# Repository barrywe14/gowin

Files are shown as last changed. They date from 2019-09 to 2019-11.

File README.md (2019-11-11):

# Gowin Project
Dokumentasi Elektronik Produk pertanian Gowin (Dropper Biji Jagung). 

# Rangkaian Elektronik Gowin
Secara general sistem elektrik Gowin
GambarElektronik
Dibawah ini adalah rangkaian di dalam kotak elektronik 
GambarHardware
Rangkaian Elektronik dalam bentuk PDF bisa [klik disini](/circuit/GoWinElectricalv2/GowinController-Controller.pdf)

## Program Arduino
Program Alat bisa klik [disini](/circuit/GoWinElectricalv1/program/GowinScript/GowinScript.ino)
Kemudian program untuk test hardware bisa klik [disini](/circuit/GoWinElectricalv1/program/GowinTestScript/GowinTestScript.ino)
# Foto Dokumentasi
Kontrol, Kotak Elektronik, dan Instrument <br>
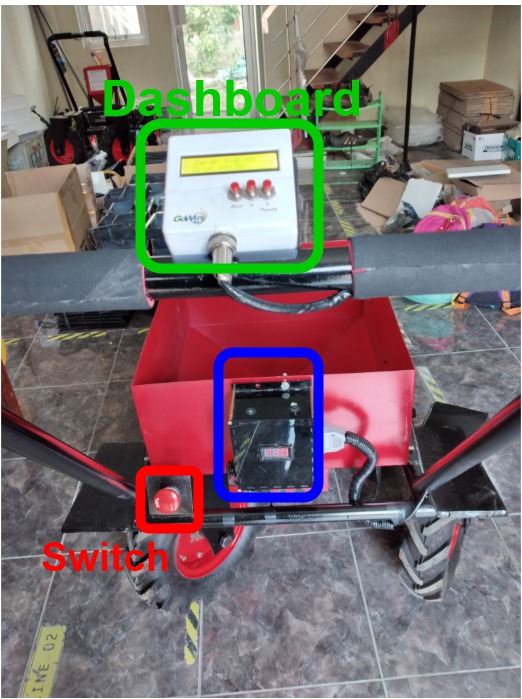
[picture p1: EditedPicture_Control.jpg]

<br>
Dropper dan encoder 
<br>
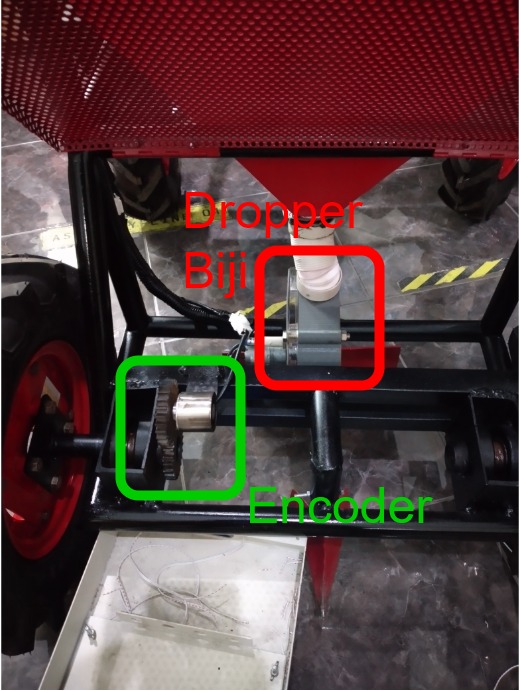
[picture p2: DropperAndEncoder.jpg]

<br>
Konektor kabel Dropper biji 
<br>
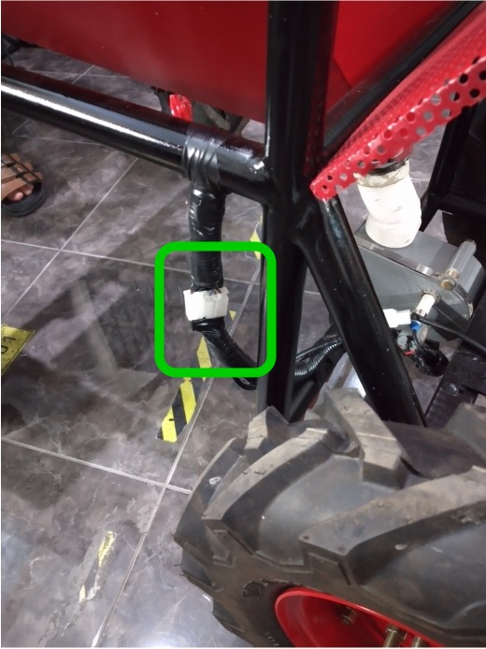
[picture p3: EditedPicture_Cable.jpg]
KabelDropper

# Cara Pemakaian
1. Putar tombol switch disebelah kotak elektronik hitam. Pastikan indikator tegangan menyala !

2. Kemudian perhatikan tampilan pada lcd, dan tunggu muncul tulisan "Gowin" maka alat mulai beroperasi. Dan ketika ada tulisan "Jarak" dan "Drop" maka peralatan telah berjalan.

3. Untuk melakukan reset, maka tekan tombol "reset" pada display.

4. Untuk melakukan pengaturan, tekan tombol "Atur". Untuk mengubah parameter kalibrasi "Tick/Biji" bisa tekan tombol  ( up ) atau tombol ( down ). Satuan yang digunakan merupakan centimeter. Dan untuk mengubah parameter yang ingin diatur, tekan lagi tombol "Atur".

5. Untuk kembali beroperasi, tekan tombol ( u) dan tombol ( down ) bersamaan
## Perhatian
- Charge baterai ketika menunjukan 8.1 V, dan jangan sampai melebihi 12V. Indikator terlihat pada kotak elektronik.
# Aplikasi Pendukung

 1. [KiCad](http://kicad-pcb.org/) sebagai pembuat skematik
 2. [draw.io](https://www.draw.io/) sebagai aplikai pembuat diagram
 3. [Arduino IDE](https://www.arduino.cc/)  sebagai IDE untuk memprogram Arduino UNO

# Partner Terlibat
UASC Manufacturing

<!--stackedit_data:
eyJoaXN0b3J5IjpbLTEzMDU3OTI3MTMsMTM5MDQ3NDI5NSwtOT
Y0OTIyNzIyLDE1NTUzMjI2NjksODQ4MjQyMDcwLDEyMTYxMDU5
NjgsLTE2MjAwMDk1MjcsLTc1NTIxMDQxOSwxNzA3NzkyODIyLC
0zNDkxMjc4MiwyMzMzOTI4MjUsMTk4Nzk2NDMzNiwxMzcwNDA3
MDMsMTM3MDQwNzAzXX0=
-->

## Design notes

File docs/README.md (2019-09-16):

# Dokumentasi Elektrik Gowin

# Shutdown System
Sistem shutdown merupakan salah satu sistem proteksi pada mobil listrik yang mengendalikan AIR (Accumulator Insulation Relay) yang terhubung dengan rangkaian traktif, dan sebagai ignition pada proses discharge pada rangkaian traktif.

## Rangkaian Sistem Shutdown
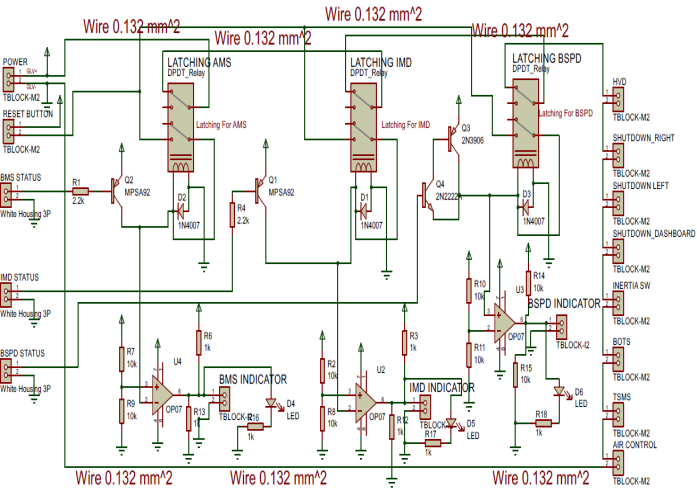
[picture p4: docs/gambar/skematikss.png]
Gambar Skematik
 <br>
Skematik pada Gambar 1 merupakan rangkaian shutdown system untuk mengendalikan kontaktor pada AIR yang terhubung dengan tractive system. Rangkaian menggunakan relay SPDT untuk interlock IMD, AMS dan BSPD. Relay diatas di drive dengan transistor pnp yang dipicu dari IMD, AMD, dan BSPD. Selanjutnya rangkaian tersebut dilengkapi dengan indikator setiap interlock, karena hanya menggunakan sebuah tombol reset. Selain interlock tersebut terdapat 7 switch yang digunakan(HVD, Shutdown right, Shutdown left, Shutdown dashboard, inertia switch, BOTS, dan TSMS) dan setiap switch terhubung Normally Close(NC). Skematik rangkaian diatas digunakan pada mobil FSAE UII untuk SFJ 2018 dan telah diuji serta layak digunakan.

> An awesome project.

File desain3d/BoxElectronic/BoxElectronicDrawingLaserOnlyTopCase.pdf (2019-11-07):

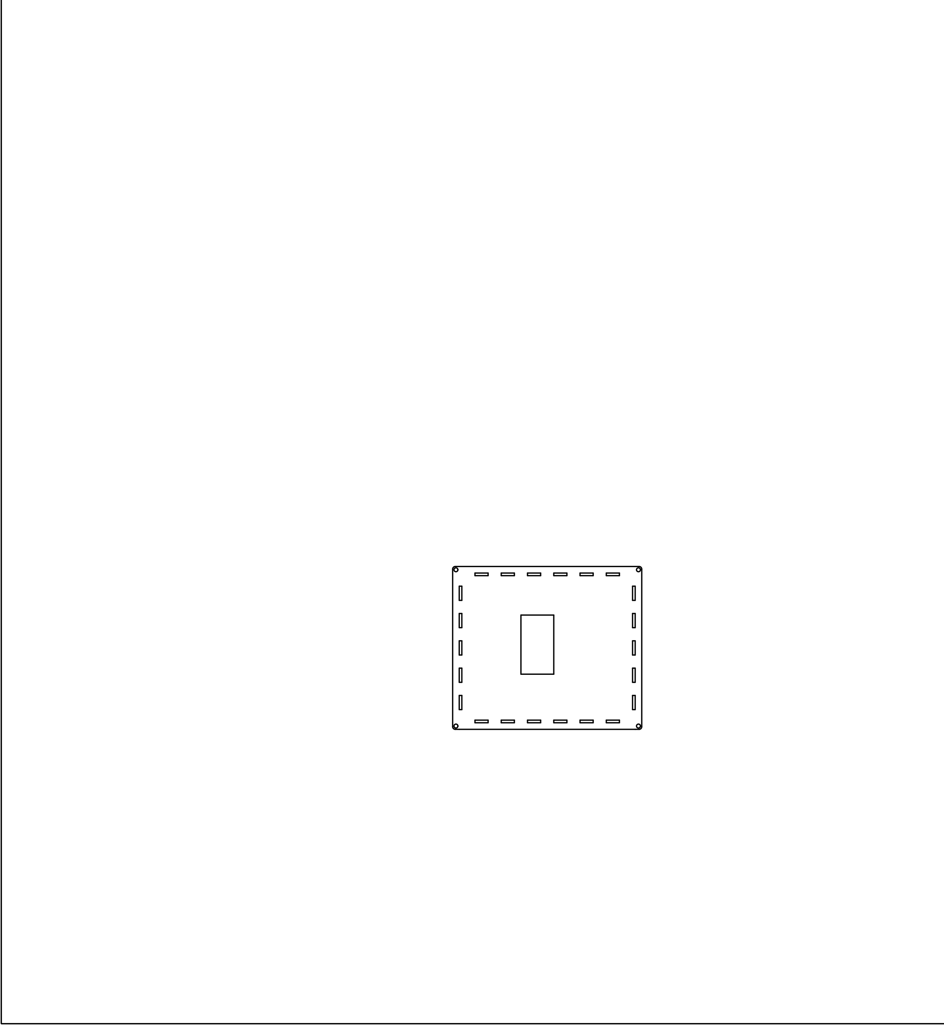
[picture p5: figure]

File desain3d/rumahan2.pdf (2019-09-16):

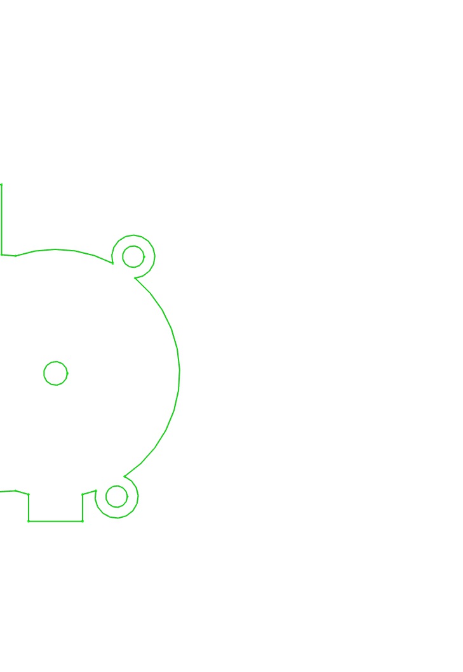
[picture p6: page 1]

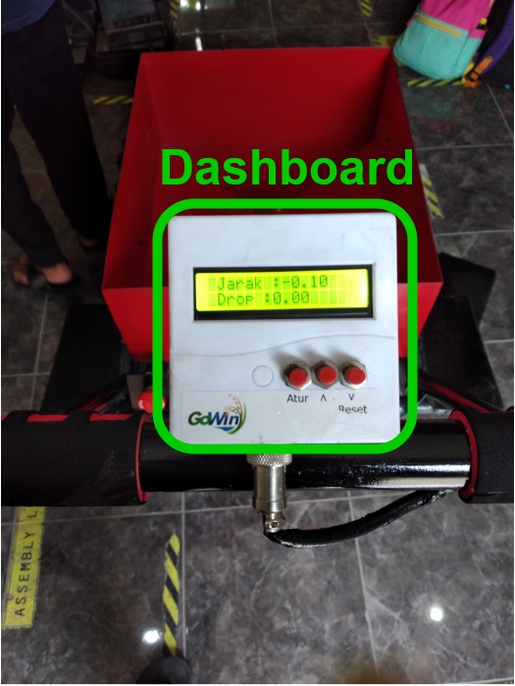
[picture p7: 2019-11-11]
EditedPicture_DashboardOnly.jpg

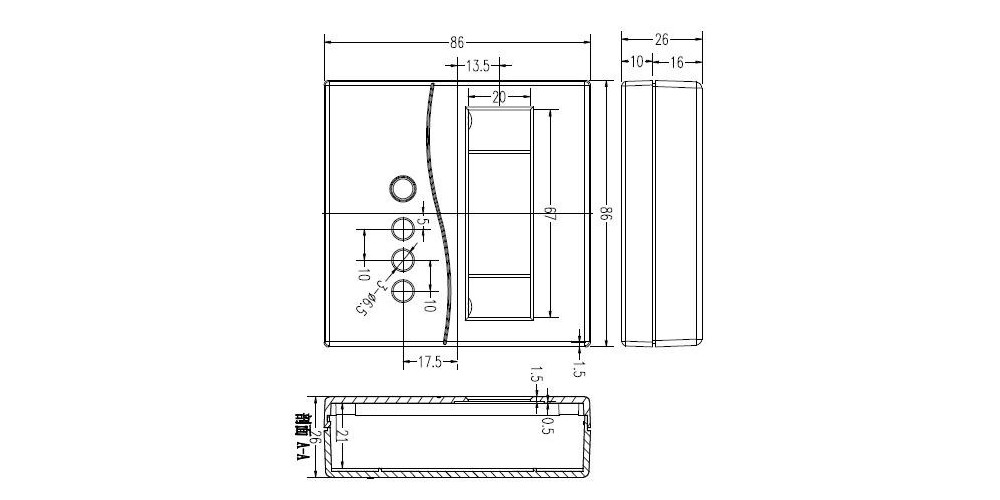
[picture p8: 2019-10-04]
BoxLCD.jpg

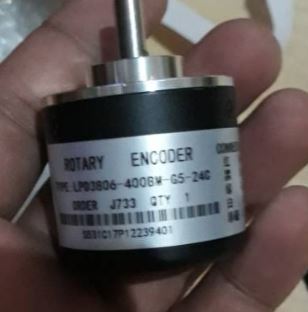
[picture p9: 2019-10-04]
desain3d/NewEncoder.JPG

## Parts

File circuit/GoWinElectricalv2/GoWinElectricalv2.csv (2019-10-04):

Id | Designator | Package | Quantity | Designation | Supplier and ref
1 | U2 | DIP-8_W7.62mm | 1 | HCPL3120
2 | XA1 | Arduino_Mini_Socket | 1 | Arduino_Mini_01_Socket
3 | D1 | D_5W_P10.16mm_Horizontal | 1 | D
4 | DashboardConn1 | Pin_Header_Straight_1x07_Pitch2.54mm | 1 | XH2.54_7p
5 | MotorConn1,BatterySupply1,DCDCConverter1 | TerminalBlock_Phoenix_MPT-2.54mm_2pol | 3 | Conn_1x2
6 | R1,R2 | R_Axial_DIN0204_L3.6mm_D1.6mm_P5.08mm_Horizontal | 2 | R
7 | RV1,RV2,RV3 | Potentiometer_Trimmer_Bourns_3296W | 3 | POT_TRIM
8 | U1 | DIP-14_W7.62mm_Socket_LongPads | 1 | LM324
9 | Q1 | TO-220-3_Vertical | 1 | IRF3205
10 | C1 | CP_Radial_D12.5mm_P5.00mm | 1 | CP
11 | Encoder1,PositionTrigger1 | Pin_Header_Straight_1x04_Pitch2.54mm | 2 | XH2.54_4p
12 | PinHeadBawah1 | Pin_Header_Straight_2x03_Pitch2.54mm | 1 | Conn_02x03_Odd_Even
13 | PinHeadKanan1,PinHeadKiri1 | Pin_Header_Straight_2x12_Pitch2.54mm | 2 | Conn_02x12_Odd_Even
14 | REF**,REF**,REF** | MountingHole_3.2mm_M3_ISO7380_Pad | 3 | MountingHole_3.2mm_M3_ISO7380_Pad

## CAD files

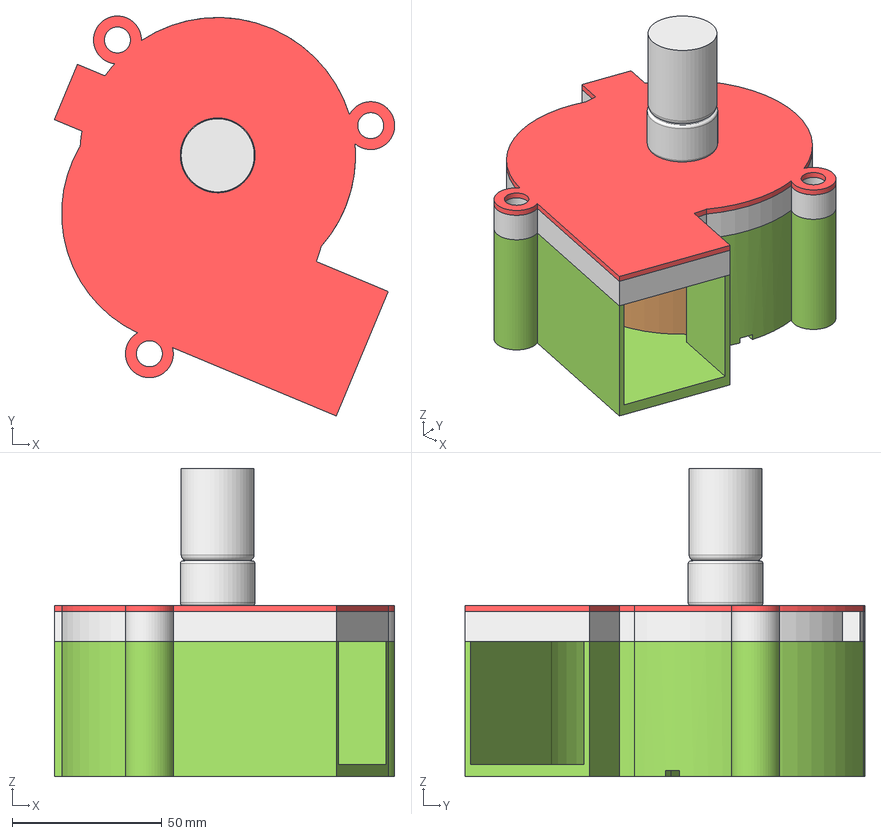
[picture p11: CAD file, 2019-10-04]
desain3d/RumahanDropperAssembly.step
113.5 x 133.4 x 102.8 mm

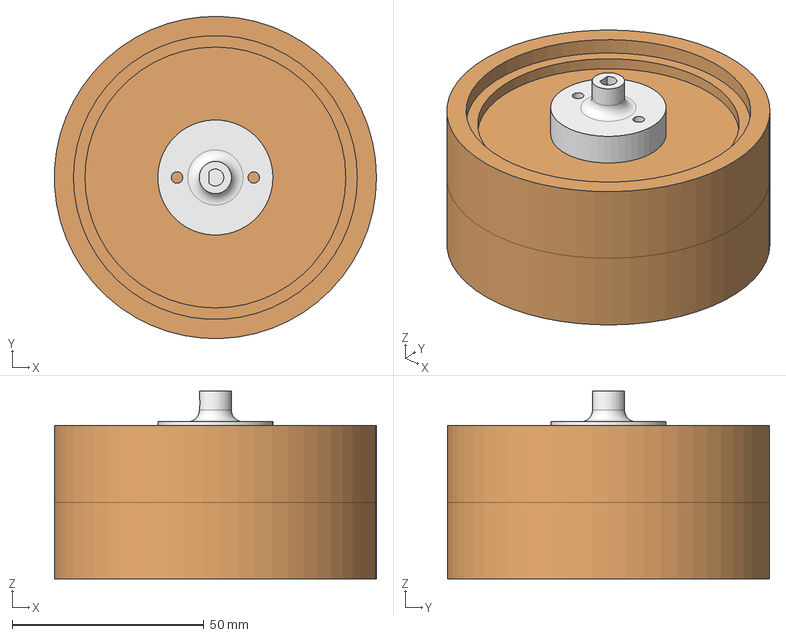
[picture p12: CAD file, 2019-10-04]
desain3d/DropperBijiAssembly.FCStd
83.9 x 84.0 x 49.0 mm
DropperBiji_001
Coupler_001

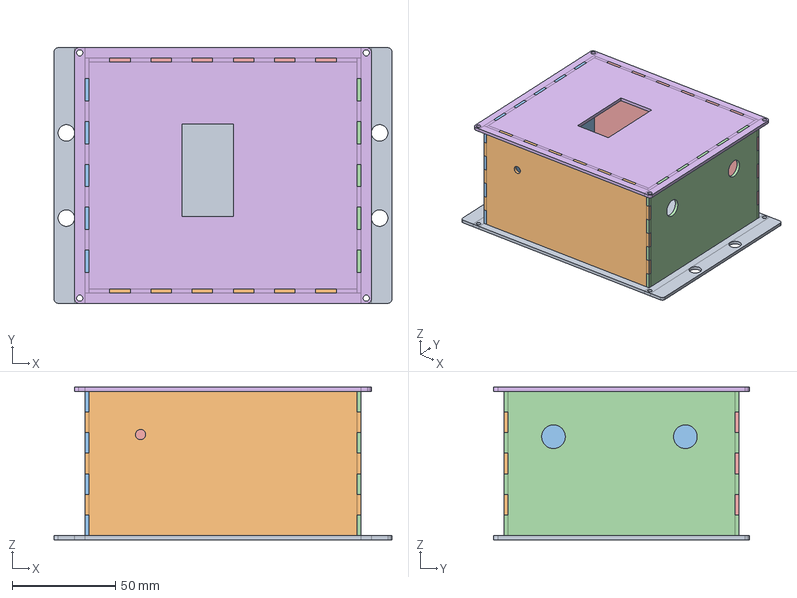
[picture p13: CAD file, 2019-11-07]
desain3d/BoxElectronic/BoxElectronicPart.FCStd
164.0 x 124.0 x 74.0 mm
AlasBox
DindingPanjang
DindingPendek
DindingPendekBolong
DindingPanjangBolong
TutupAtas

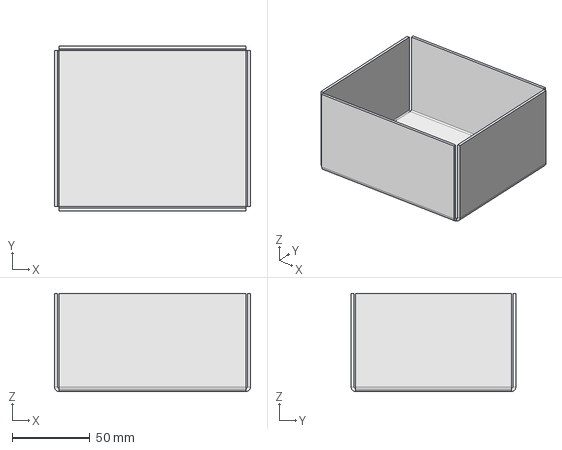
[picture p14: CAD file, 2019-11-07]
desain3d/ElectronicBox.FCStd
126.0 x 106.0 x 63.0 mm

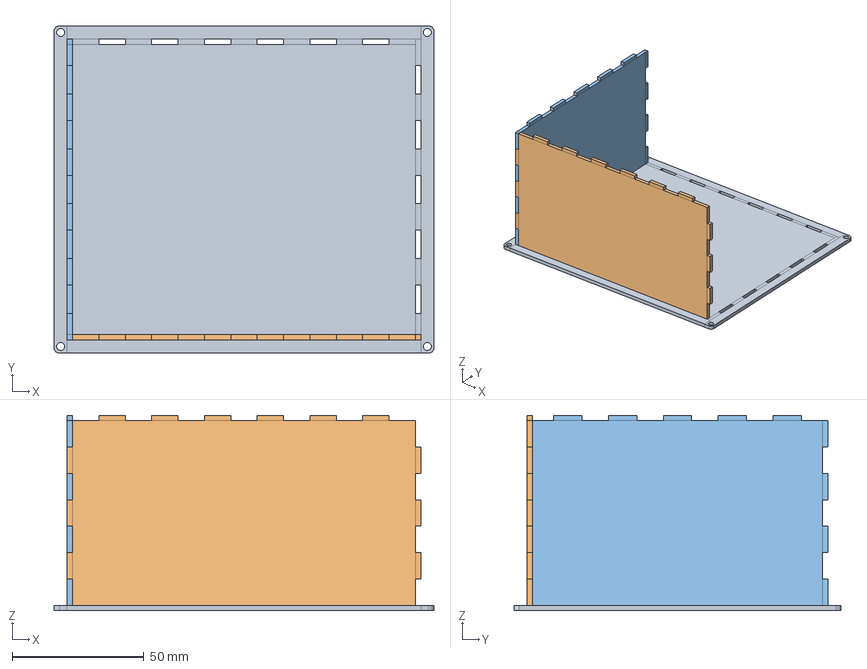
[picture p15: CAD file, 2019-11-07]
desain3d/BoxElectronic.FCStd
144.0 x 124.0 x 74.0 mm
DindingPanjang
DindingPendek

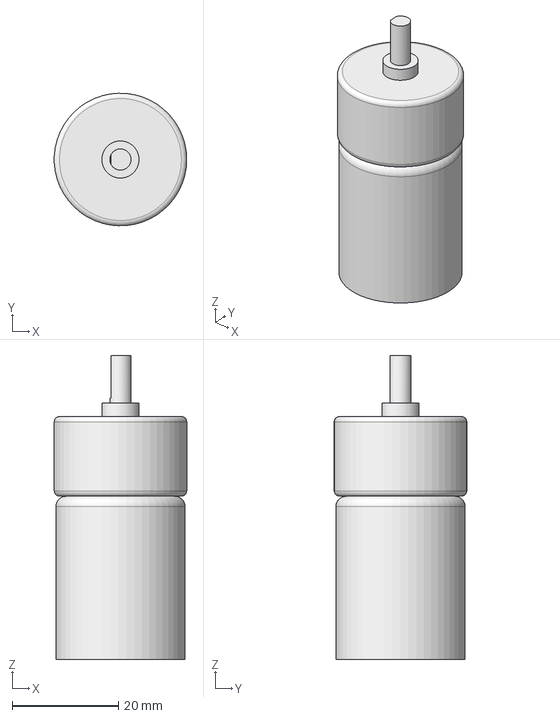
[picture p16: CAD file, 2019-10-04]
desain3d/MotorDC.FCStd
25.0 x 25.0 x 57.3 mm

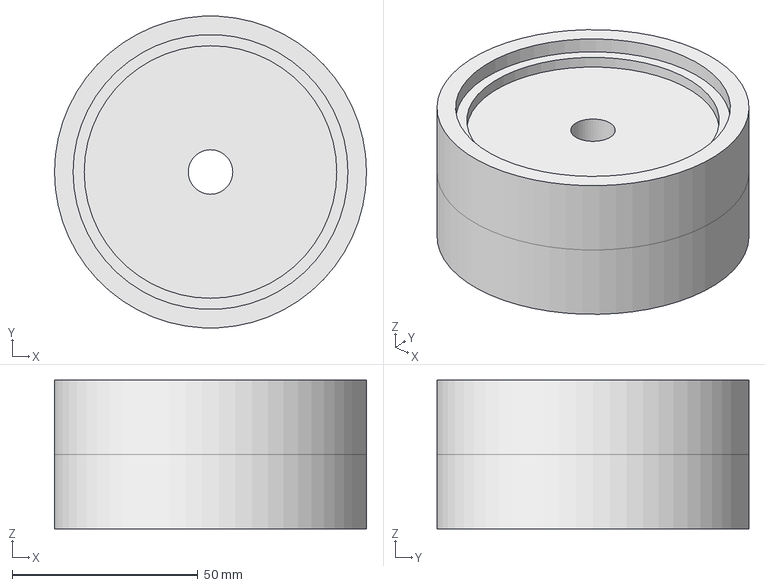
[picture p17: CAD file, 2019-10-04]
desain3d/DropperBiji.FCStd
84.0 x 83.9 x 40.0 mm

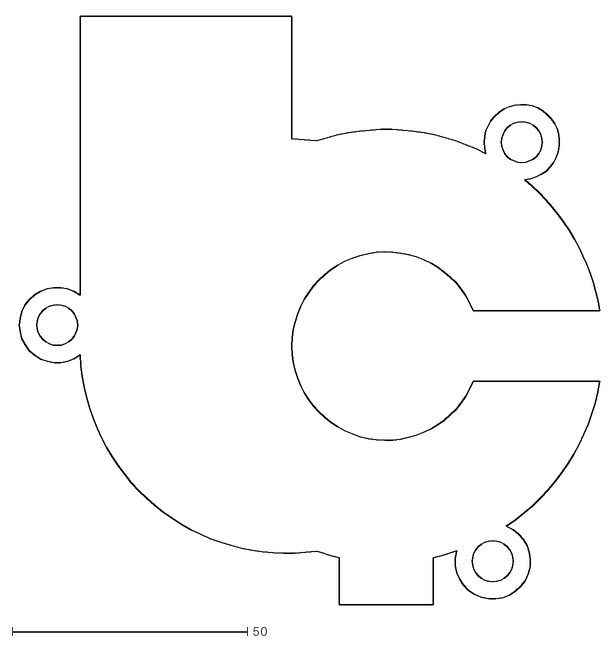
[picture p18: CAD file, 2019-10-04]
desain3d/Akrilik.dxf
124.0 x 124.9

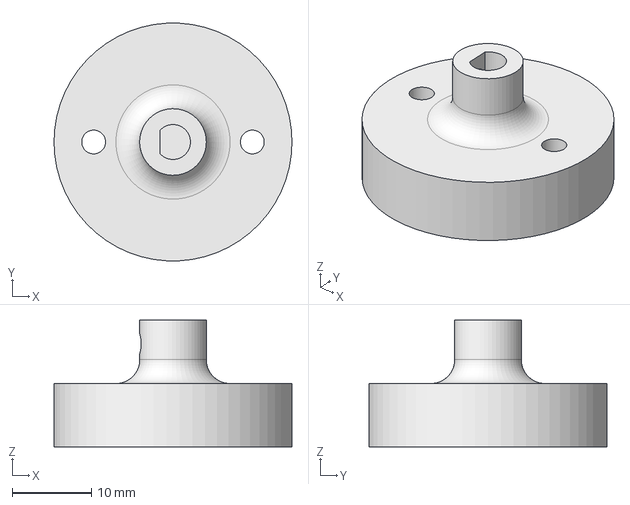
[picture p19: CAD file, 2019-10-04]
desain3d/Coupler.FCStd
30.0 x 30.0 x 16.0 mm

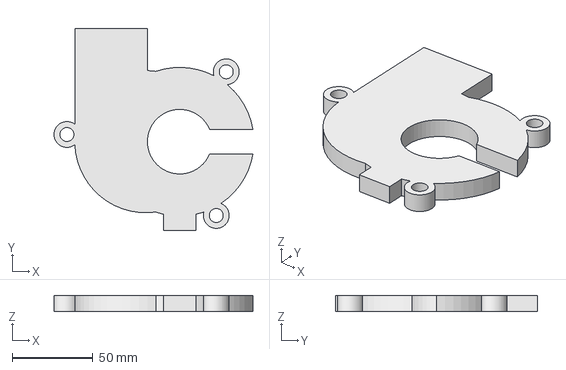
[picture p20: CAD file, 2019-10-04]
desain3d/rumahanDropperBiji_Akrilik.FCStd
123.2 x 124.9 x 10.0 mm

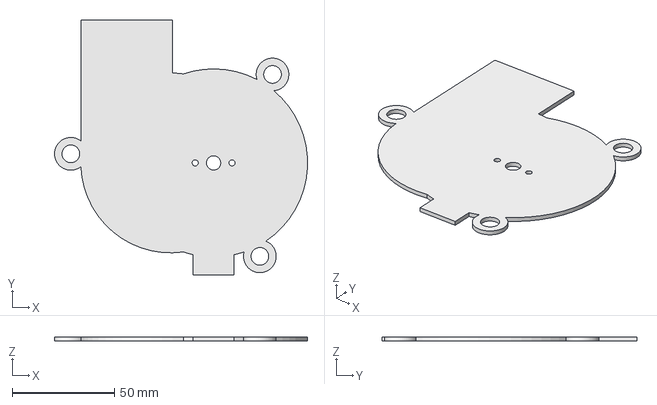
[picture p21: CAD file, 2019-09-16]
desain3d/rumahanDropperBiji.FCStd
123.8 x 124.9 x 2.00 mm

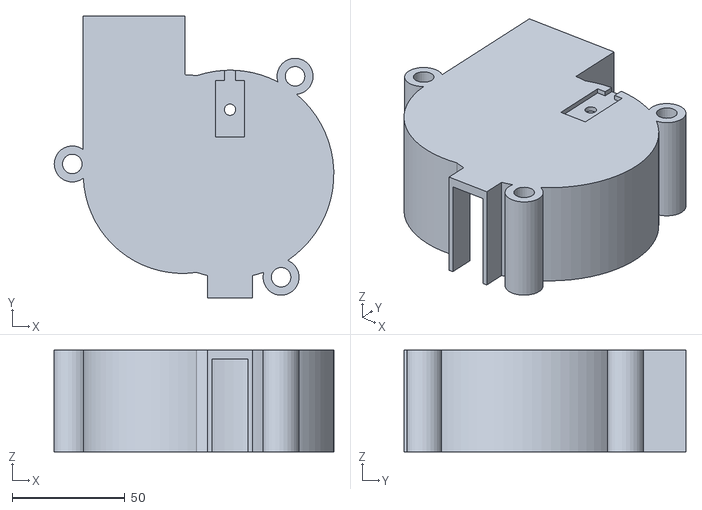
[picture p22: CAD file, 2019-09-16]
desain3d/rumahanDropperBiji2Terbaru.stl
123.8 x 124.9 x 45.0

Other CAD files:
desain3d/BoxElectronic/BoxElectronicAssembly.FCStd
desain3d/RumahanAssembly.FCStd
desain3d/encoder.FCStd
desain3d/coupler3.stl
desain3d/rumahanDropperBiji2.FCStd
desain3d/RumahanDropperBiji_DudukanMotor.step
desain3d/coupler.stl
desain3d/coupler2.stl
desain3d/rumahanDropperBiji.stl

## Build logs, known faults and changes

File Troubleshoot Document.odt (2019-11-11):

# GOWIN PROJECT TROUBLESHOOT

## Gowin’s Project Issue :

Tanggal Mulai | Issue | Tanggal Solusi
1 Nov 2019 | Issue Name : Proximity Switch gak mau detect Kemungkinan kesalahan : Ada kabel tak terhubung Aksi yang harus dilakukan : Review kabelnya kembali | 4 Nov 2019 Telah diperbaiki

5 Nov 2019

Issue Name :

1. Encoder gak mau terdeteksi pulsenya
2. Tombol 1 (Atur) tidak mau respons.
3. Motor Gak jalan
4. Baterai Belum Dicharge

Kemungkinan kesalahan :

1. Kabel Putus, tidak terhubung. Ada Socket yang tak terhubung. Kabel putus di dalam rangka. Untuk issue (1,2,3)
2. Encoder Rusak. Untuk issue (1)
3. kesalahan rangkaian penanganan sinyal pada kontroller. Untuk issue (1)
4. Kurang tegangan. Untuk issue (1,3)

Aksi yang harus dilakukan :

1. untuk kesalahan pada nomor (1), cek semua kabel dengan menggunakan multimeter mode buzzer. Titik ukur pada setiap ujung kabel
2. Coba cek menggunakan oscciloscope, dengan titik ukur pada kontrollernya.
3. untuk kesalahan pada nomor (3), melakukan perbaikan pada kontroller bisa menggunakan alternatif rangkaian seperti pada lampiran 1
4. untuk issue(4) dan kesalahan (4)

Indikator Selesai :

1. semua sensor , terutama encoder bekerja dengan baik
2. Baterai telah dicharge, atau diatas 11 volt

8 Nov 2019
Telah Diperbaiki

Solusi :

Sinyal encoder di putus dari op-amp (ada di dokumentasi) dan langsung di pullup internal pada arduino.

Kabelnya telah diperbaiki semua, sehingga dapat berjalan dengan baik
11/11/19 | Issue Name : Dropper biji jagung jatuh seberapa, tapi tidak tepat sesuai dengan yang diskenariokan. Kemungkinan kesalahan : Desain di dalam dropper biji yang tidak dapat langsung ke roda lubang Aksi yang harus dilakukan : Membuat ruang baru pada desain dropper biji Membuat model baru untuk dropper bijinya. Indikator Selesai : Dropperbiji jatuh sesuai dengan yang diskenario kan.

## LAMPIRAN

### Alternatif Rangkaian Encoder

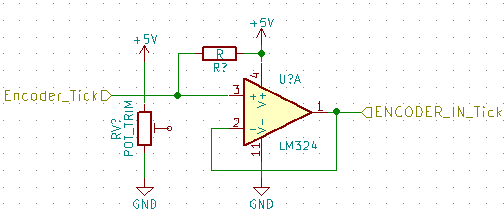
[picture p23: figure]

Gambar 1: Alternatif rangkaian encoder pada kontroller

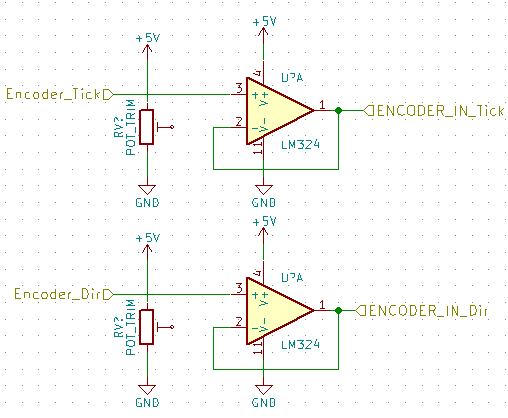
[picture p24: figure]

Gambar 2: Alternatif 2 Rangkaian encoder

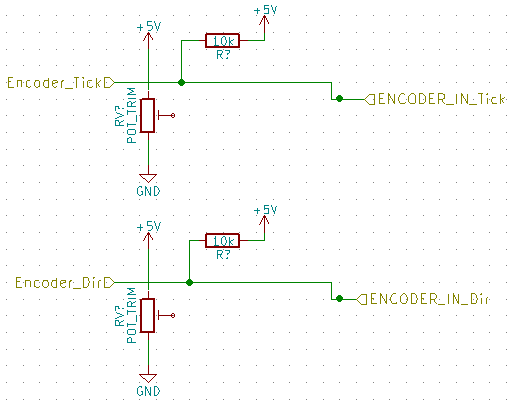
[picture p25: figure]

Gambar 3: Alternatif 3 rangkaian encoder

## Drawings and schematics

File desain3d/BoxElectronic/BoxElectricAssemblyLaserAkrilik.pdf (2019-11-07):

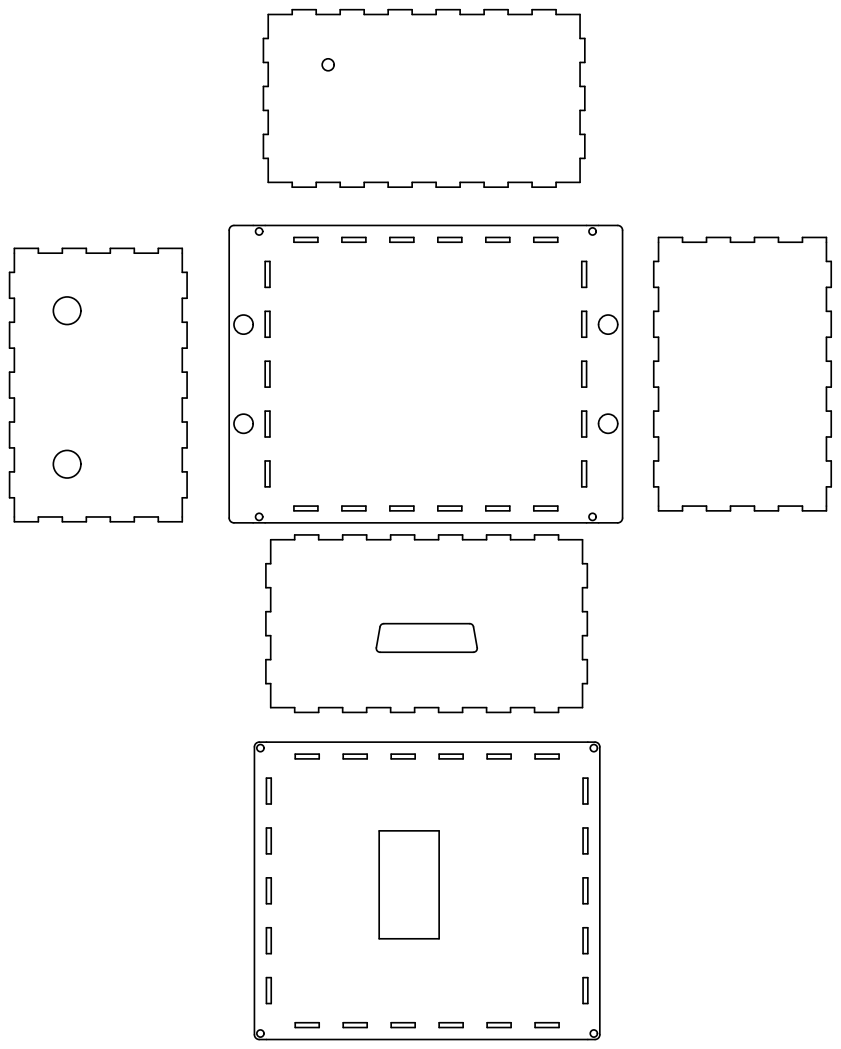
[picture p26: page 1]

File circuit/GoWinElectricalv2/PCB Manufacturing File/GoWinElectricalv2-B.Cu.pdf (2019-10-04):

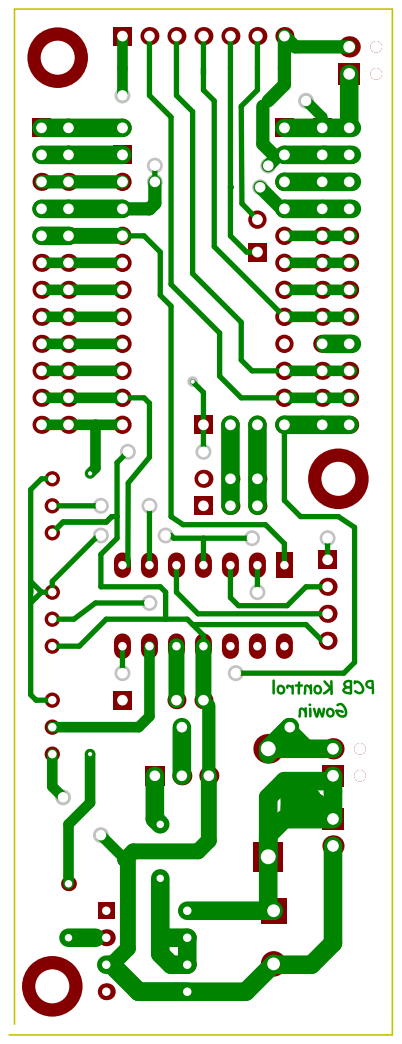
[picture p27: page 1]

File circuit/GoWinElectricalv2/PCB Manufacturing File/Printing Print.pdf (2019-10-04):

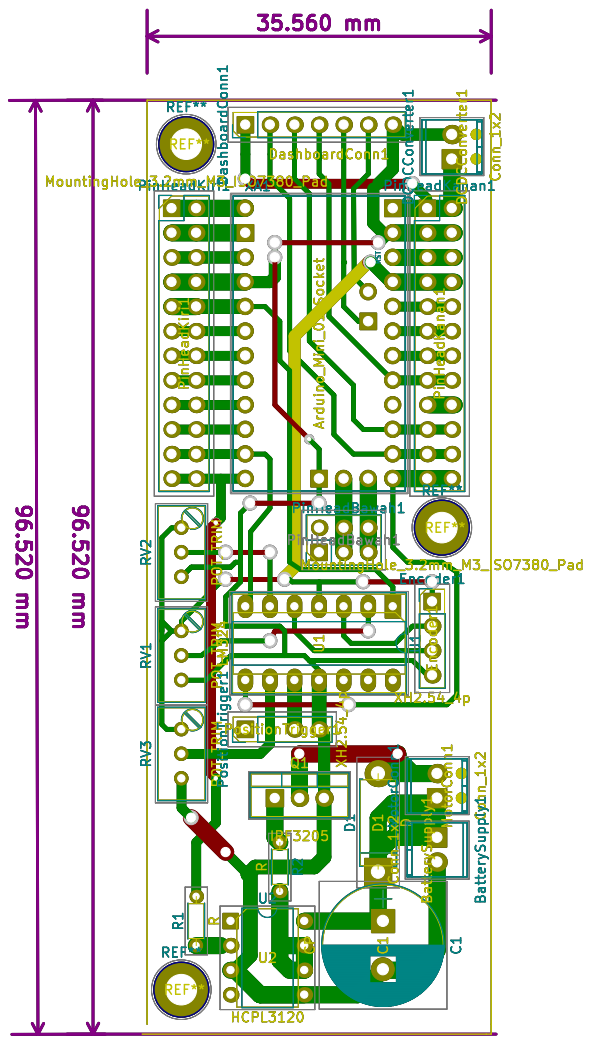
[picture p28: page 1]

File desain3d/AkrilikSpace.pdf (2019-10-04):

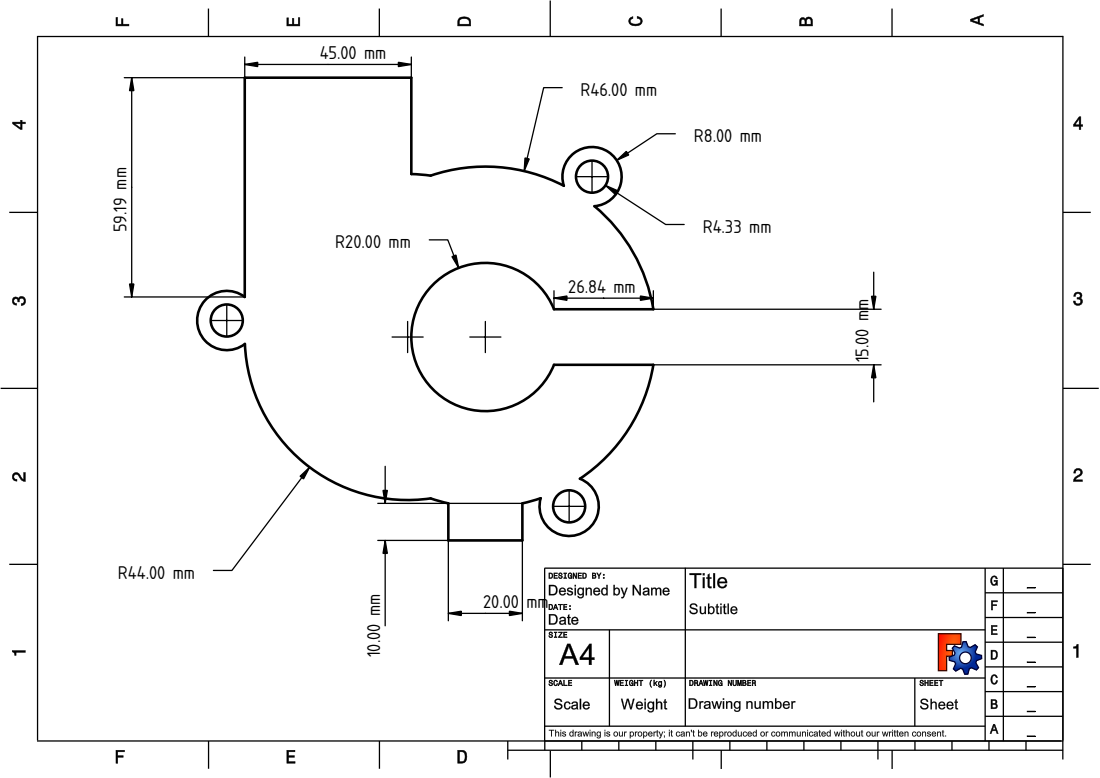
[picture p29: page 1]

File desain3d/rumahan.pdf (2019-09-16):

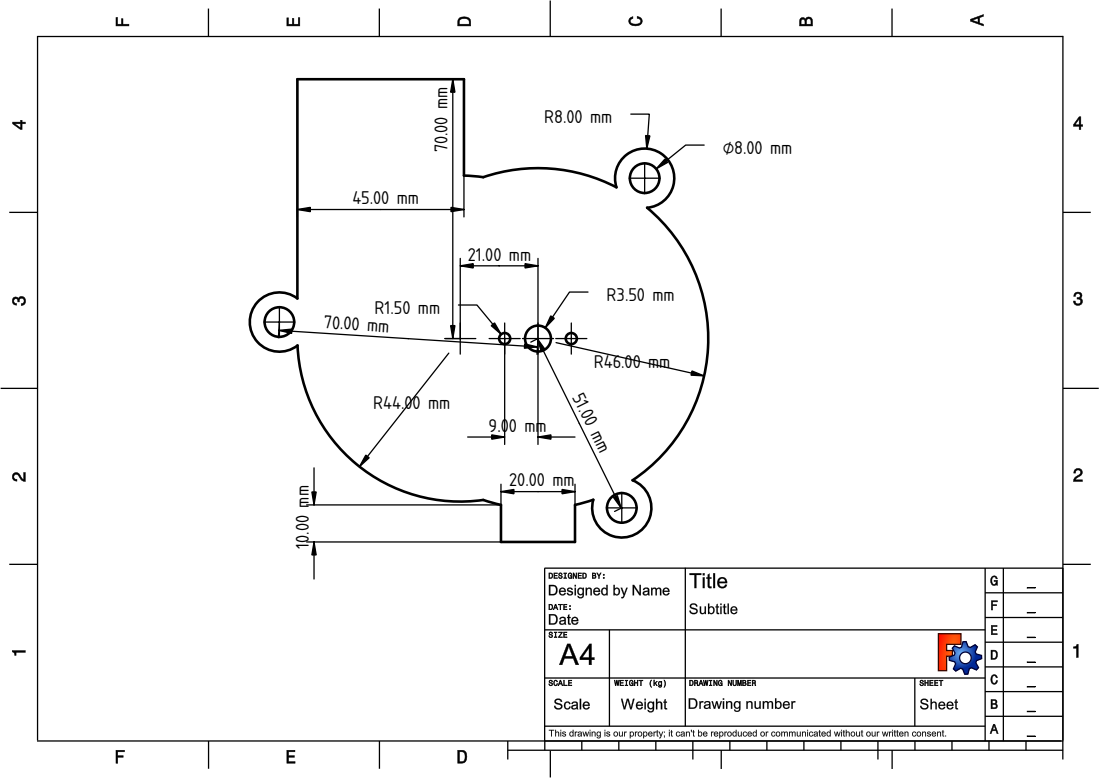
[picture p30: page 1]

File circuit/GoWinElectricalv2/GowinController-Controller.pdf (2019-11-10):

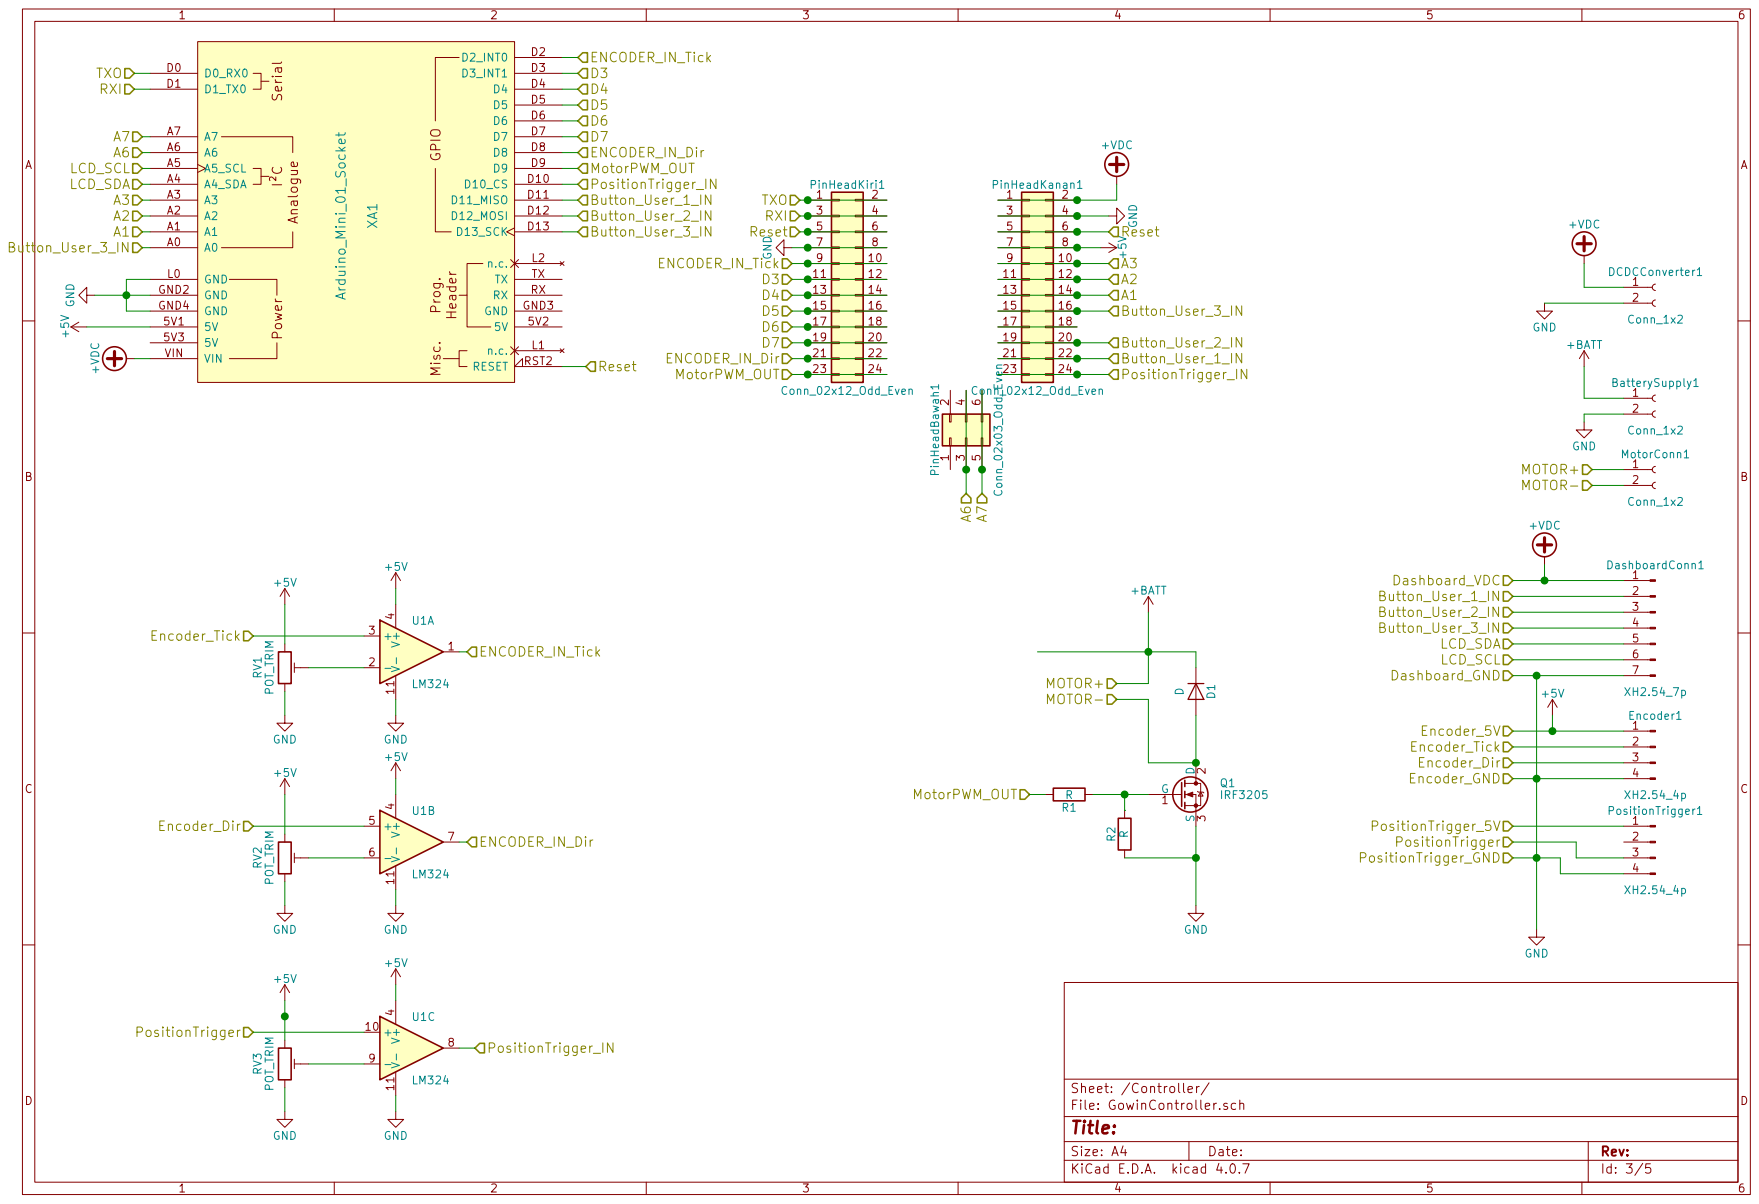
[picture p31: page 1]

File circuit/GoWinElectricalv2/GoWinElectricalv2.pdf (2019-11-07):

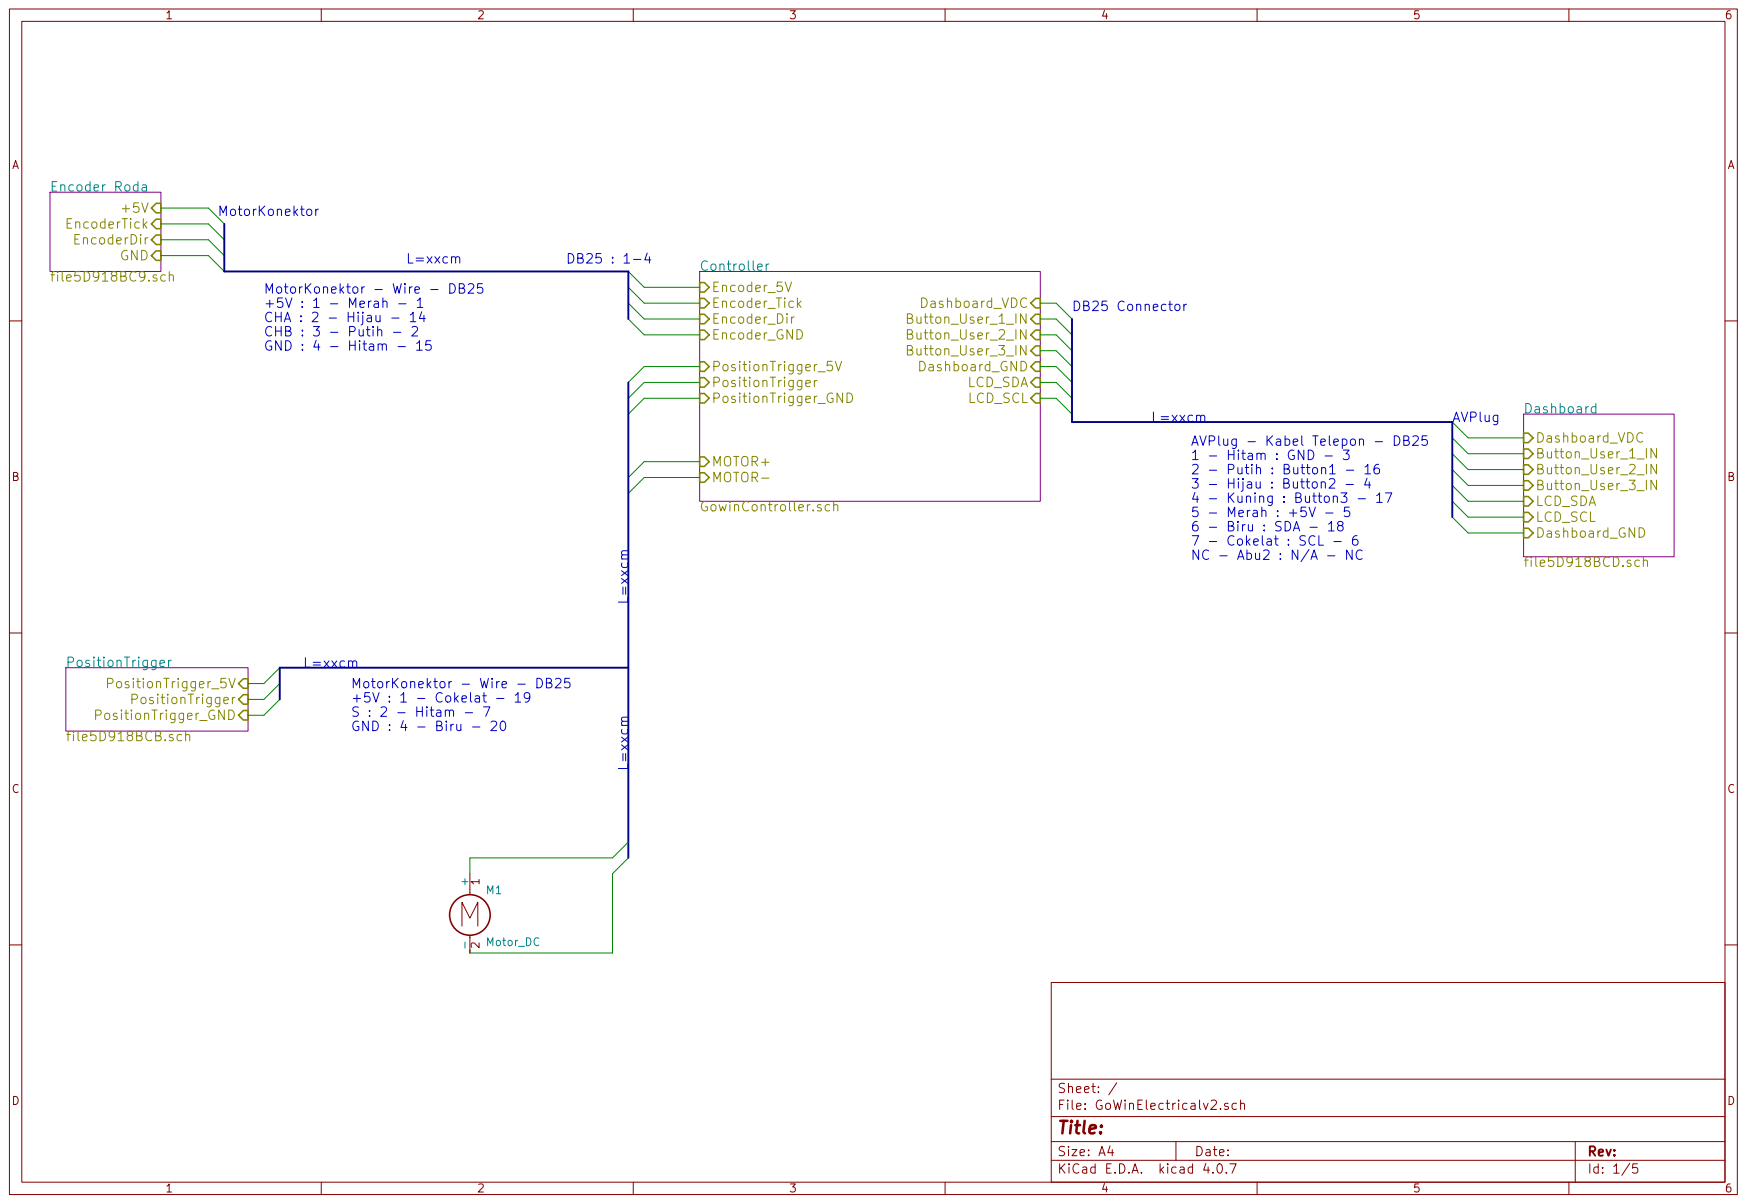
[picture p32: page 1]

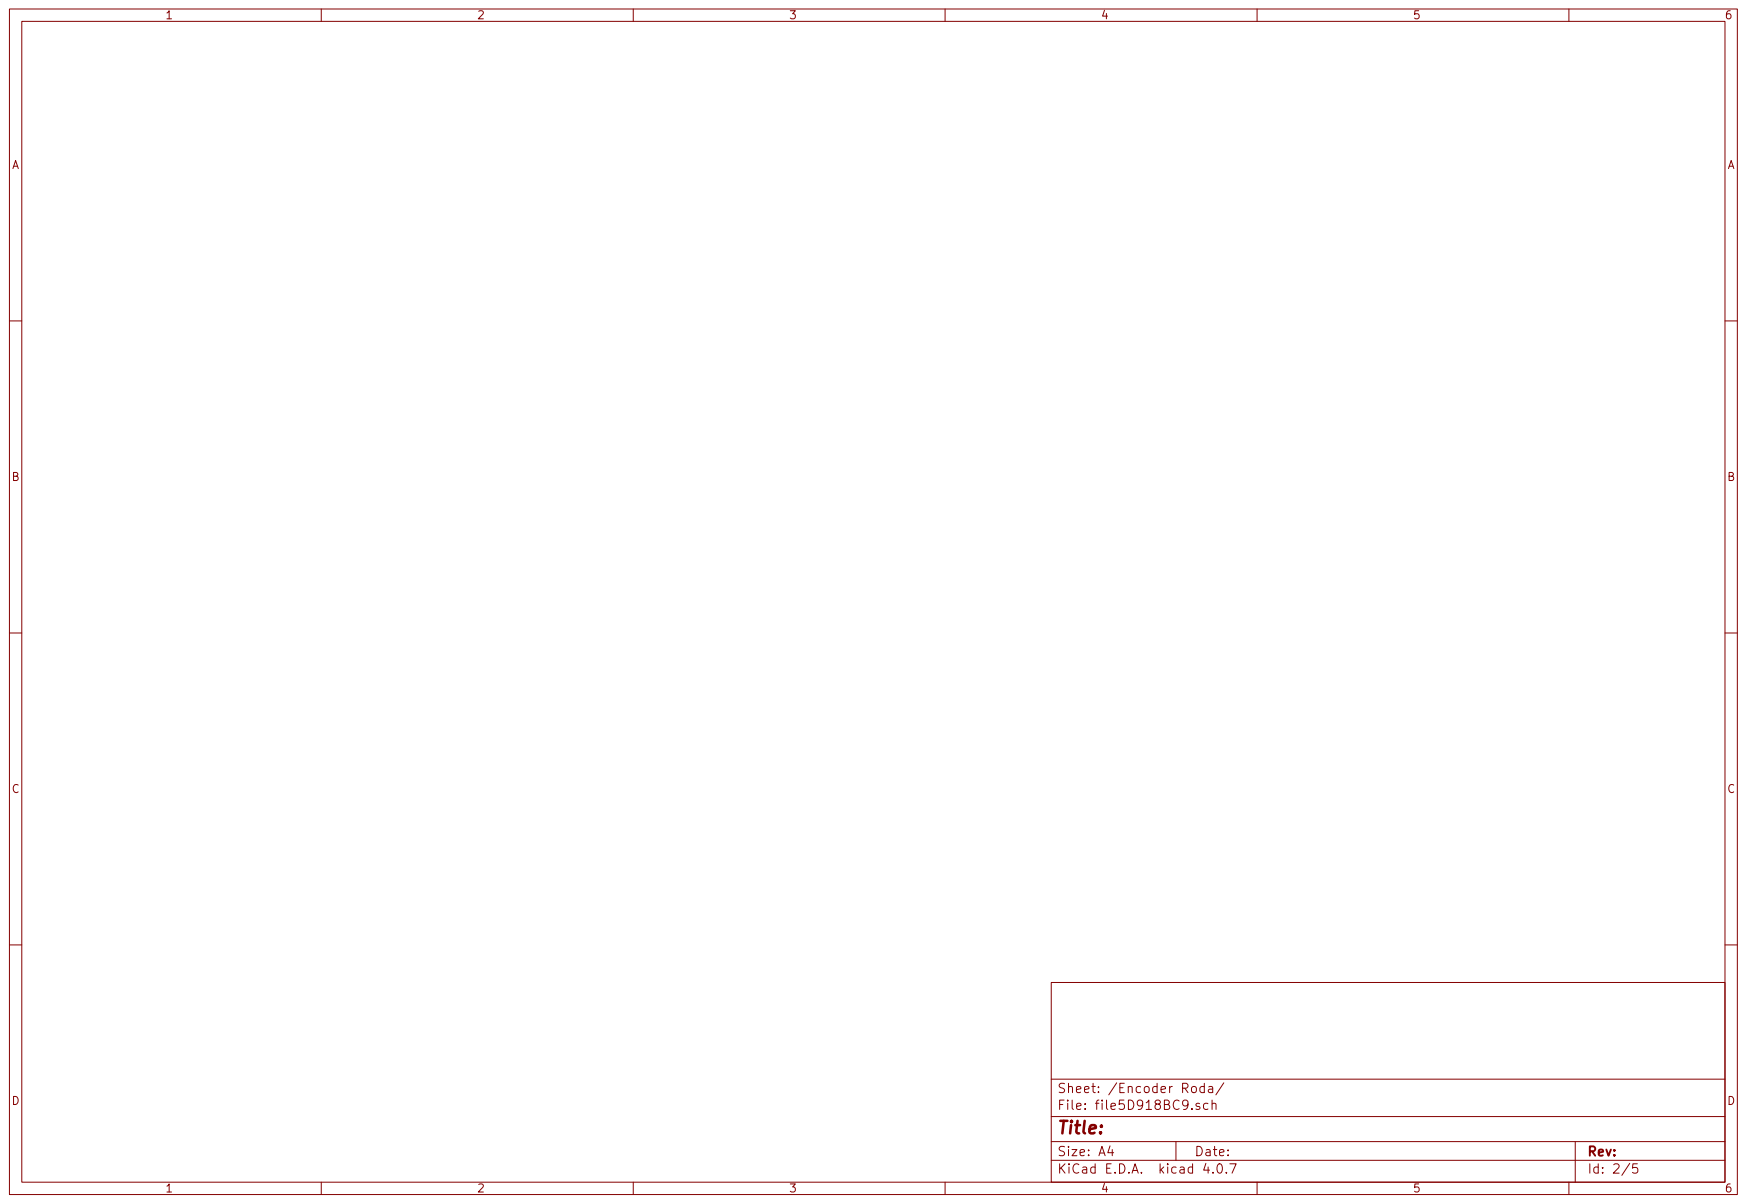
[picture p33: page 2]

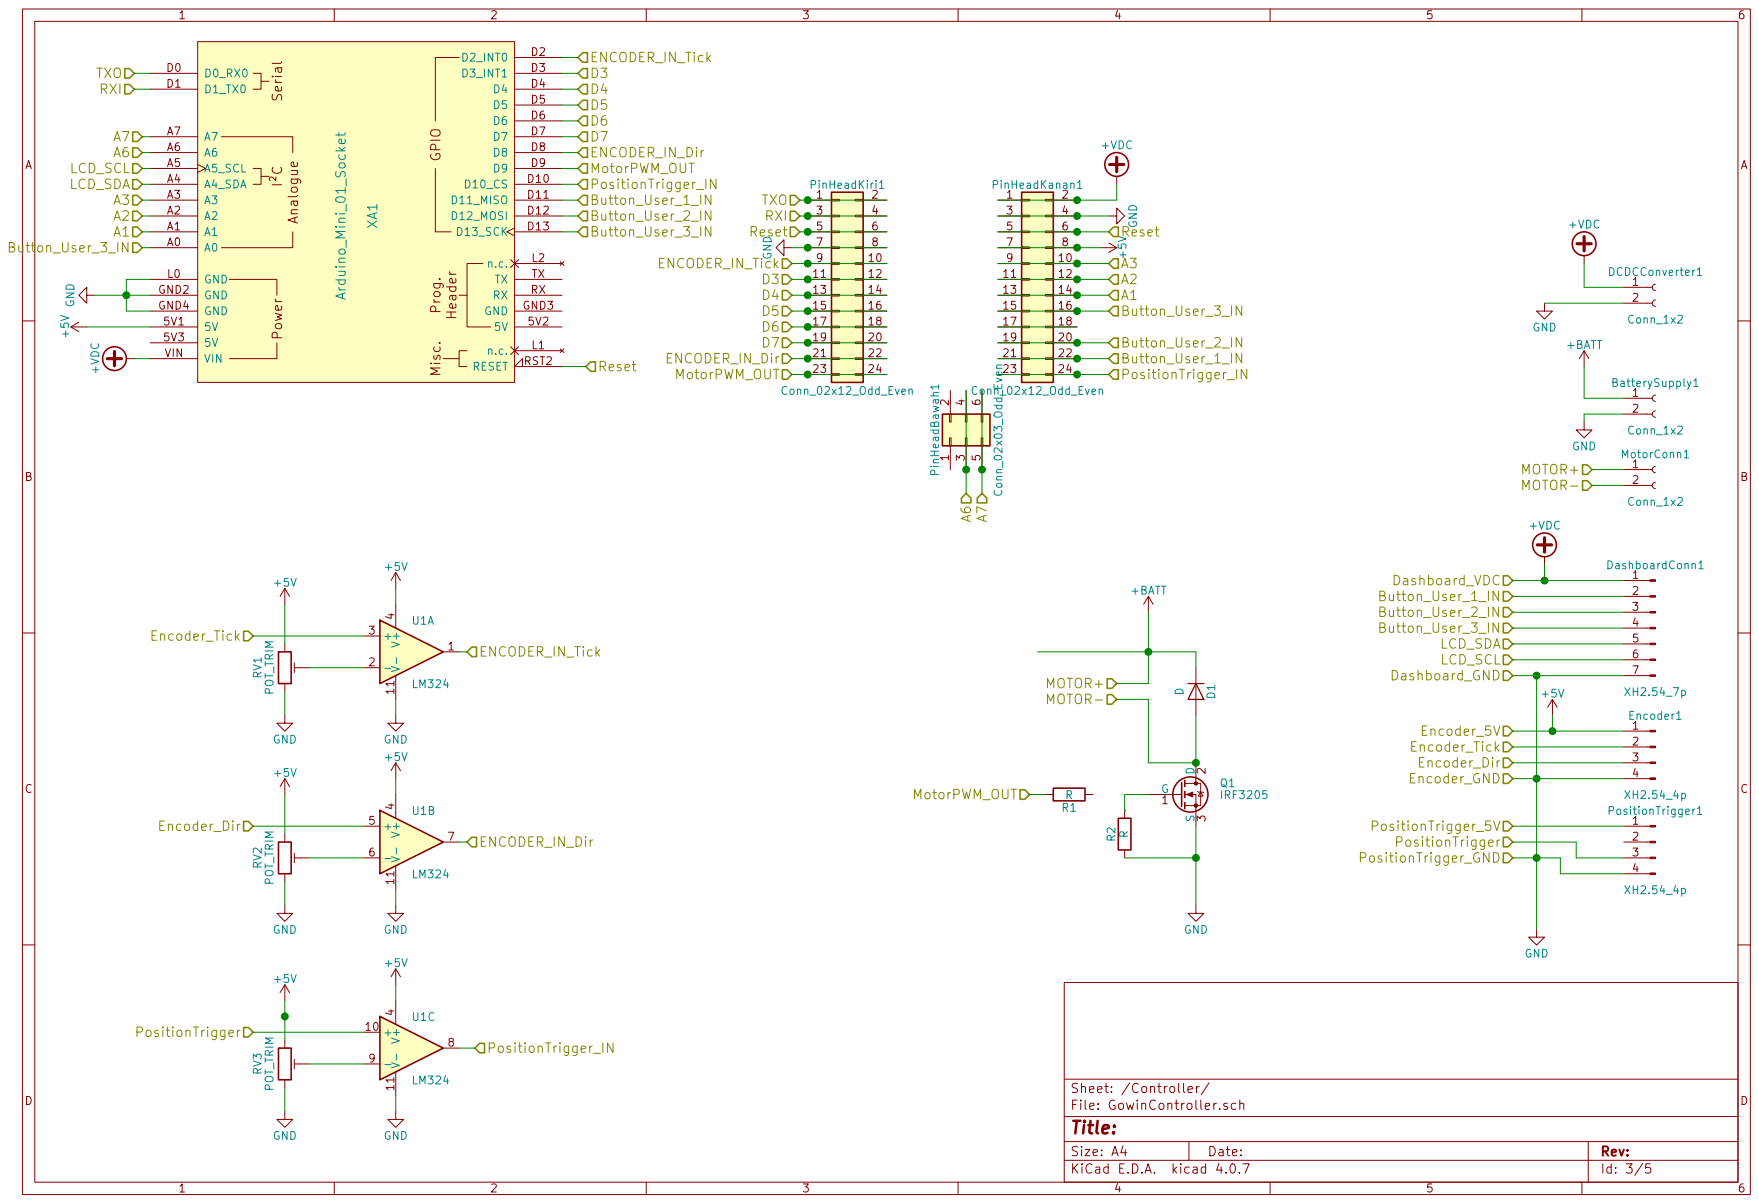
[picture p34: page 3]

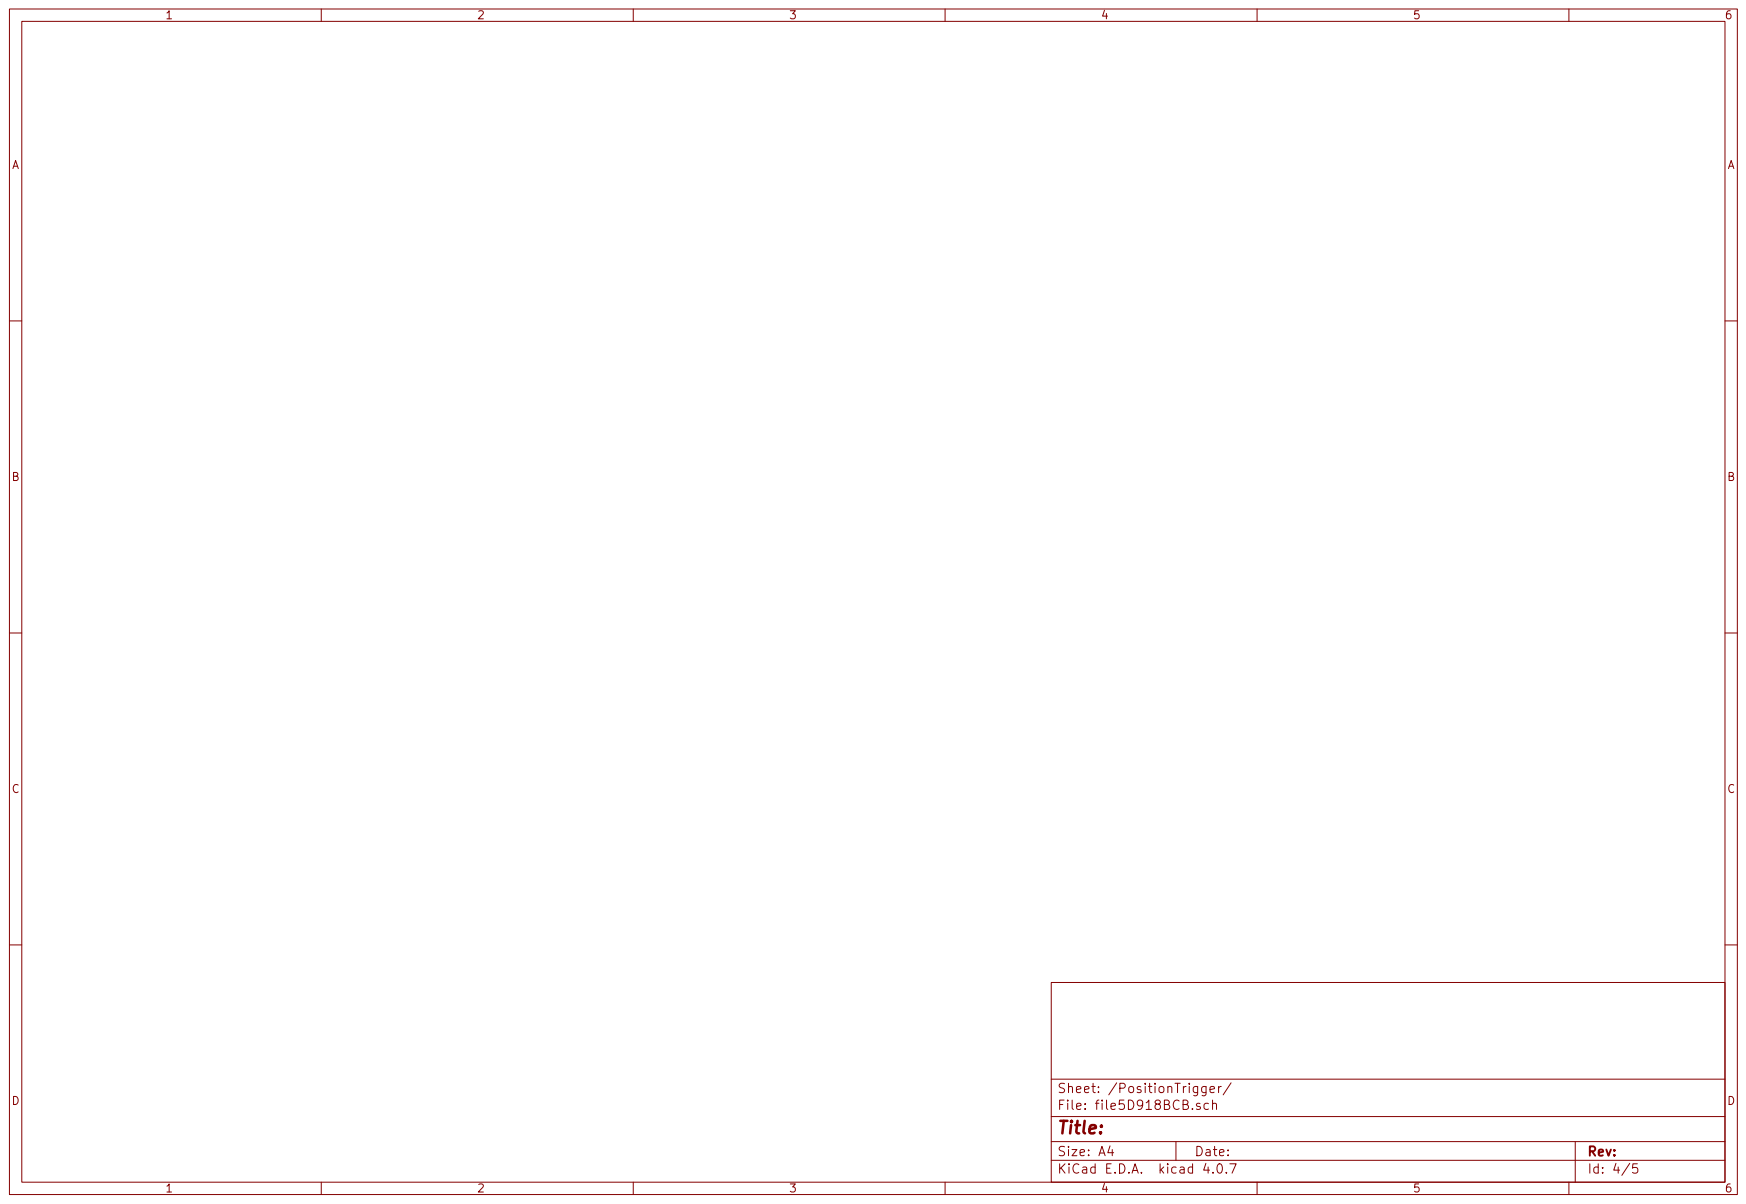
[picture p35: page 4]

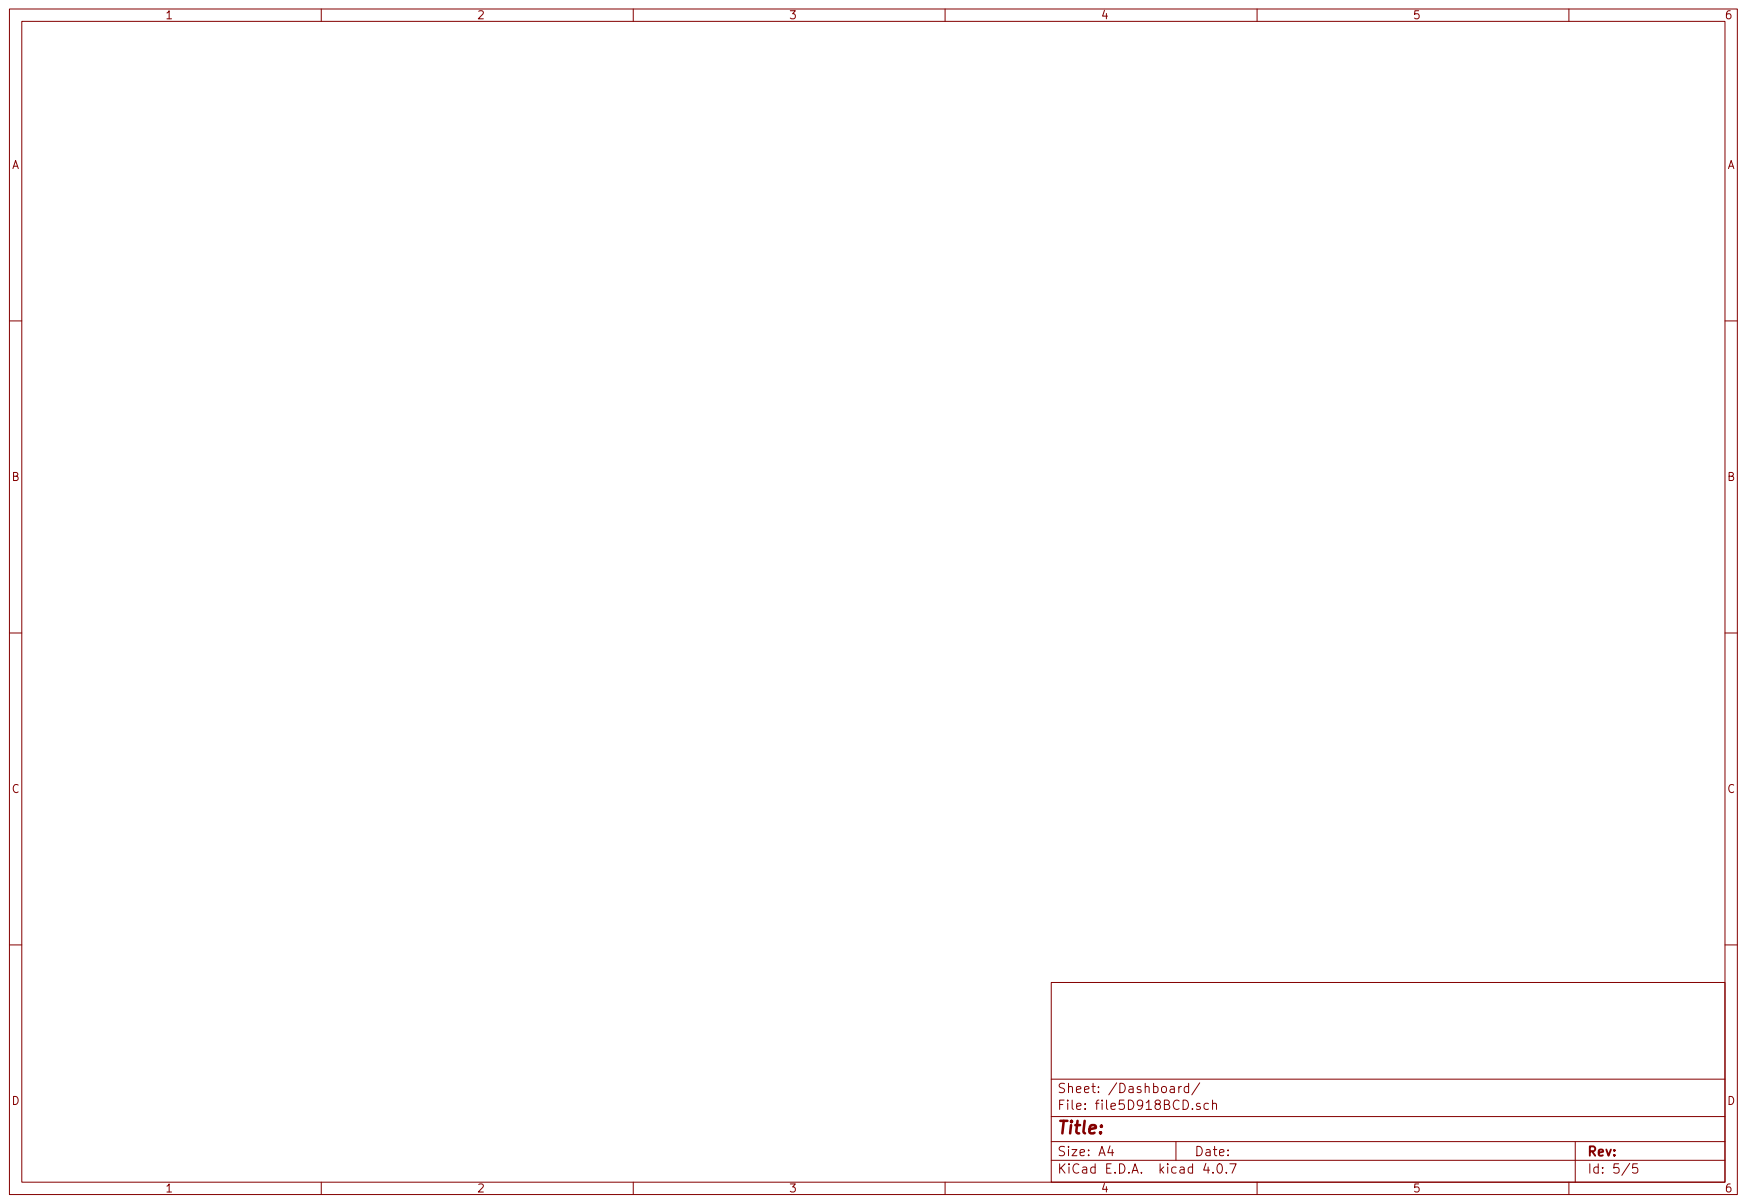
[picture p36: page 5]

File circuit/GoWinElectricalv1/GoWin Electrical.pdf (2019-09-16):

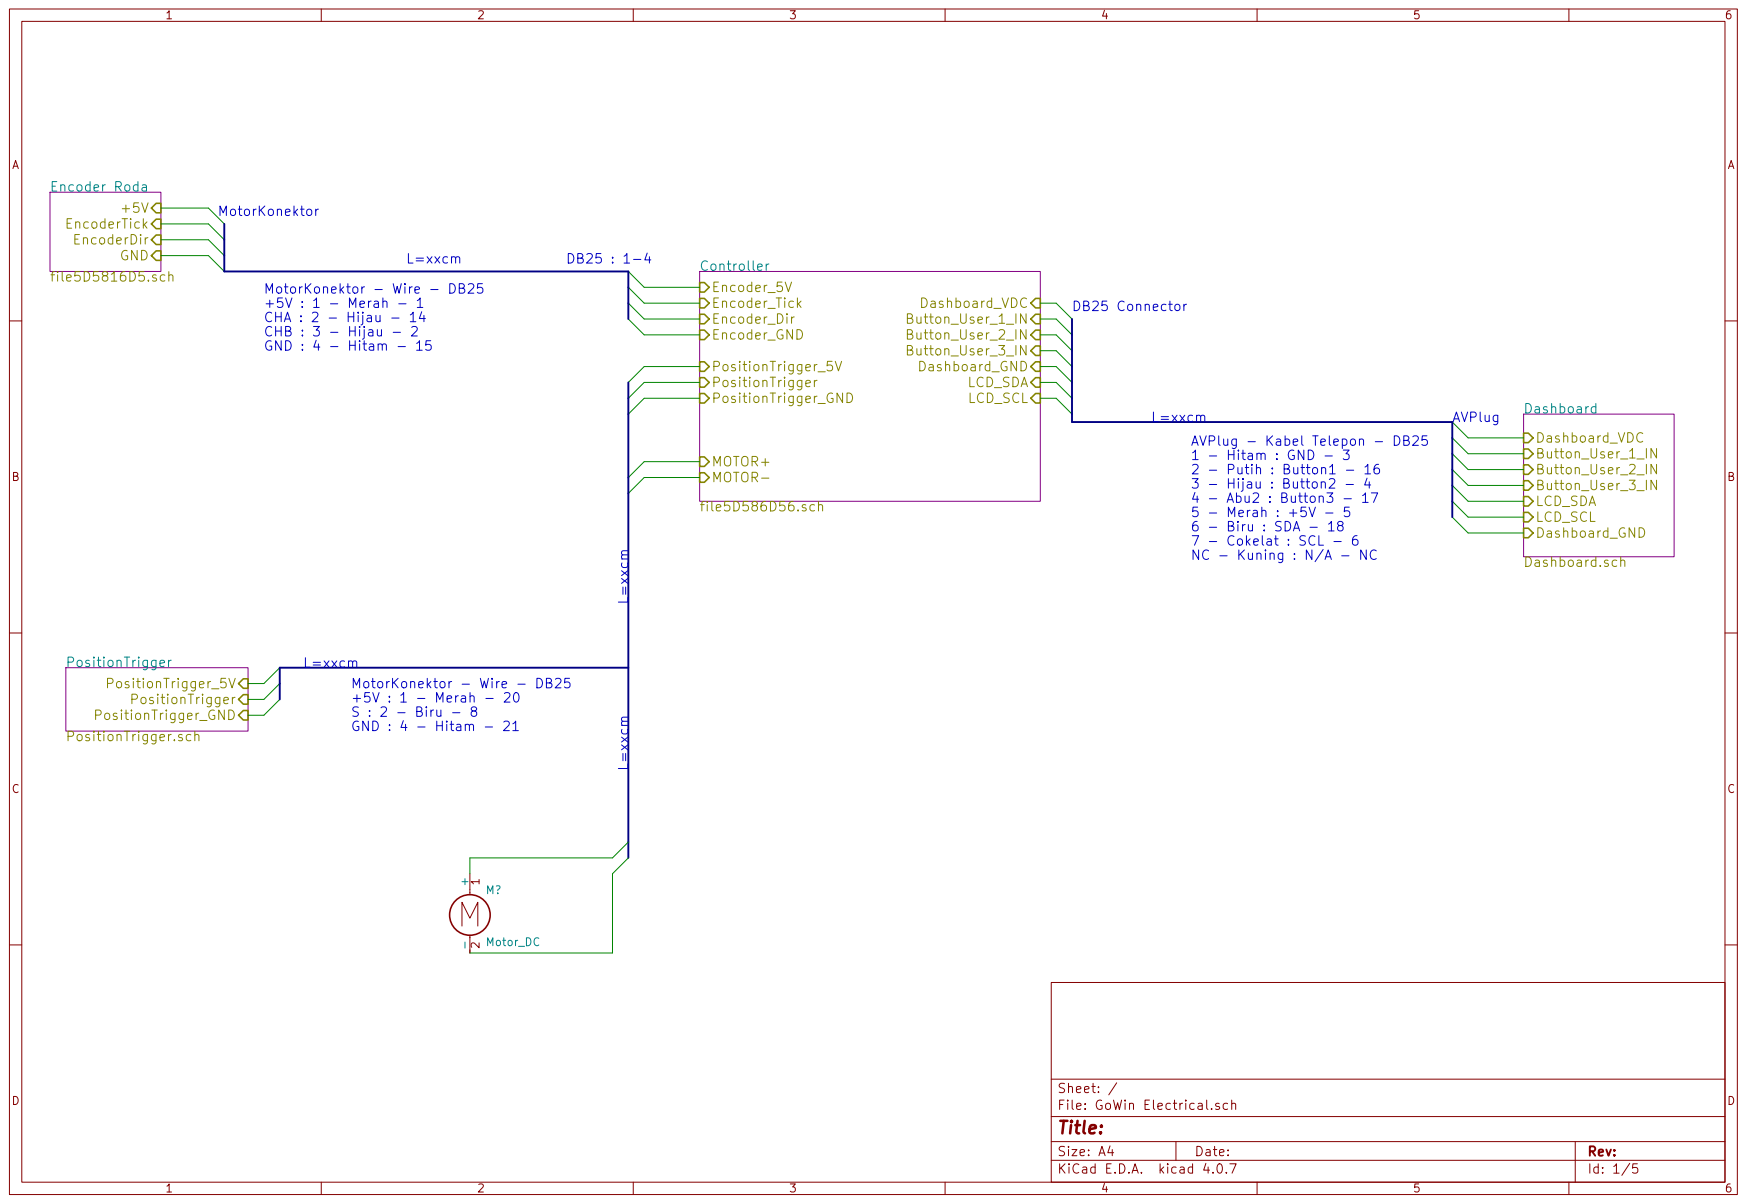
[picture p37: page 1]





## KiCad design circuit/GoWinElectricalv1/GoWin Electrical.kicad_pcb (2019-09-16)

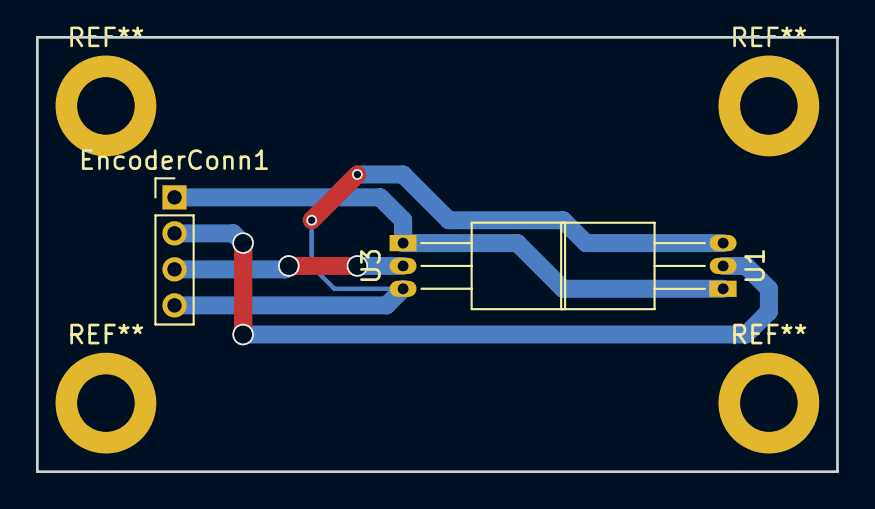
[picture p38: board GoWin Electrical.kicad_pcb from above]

Board: 2 copper layers, 44.5 x 24.1 mm, 3 parts (0 on the bottom side), 4 nets.

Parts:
EncoderConn1: Conn_01x04_Female; Pin_Header_Straight_1x04_Pitch2.00mm
U1, U3: A1301KLHLT-T; TO-92_Horizontal2_Inline_Narrow_Oval

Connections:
+5V: EncoderConn1.1, U1.1, U3.1
/Encoder Roda/EncoderDir: EncoderConn1.3, U3.2
Encoder: EncoderConn1.2, U1.2
GND: EncoderConn1.4, U1.3, U3.3

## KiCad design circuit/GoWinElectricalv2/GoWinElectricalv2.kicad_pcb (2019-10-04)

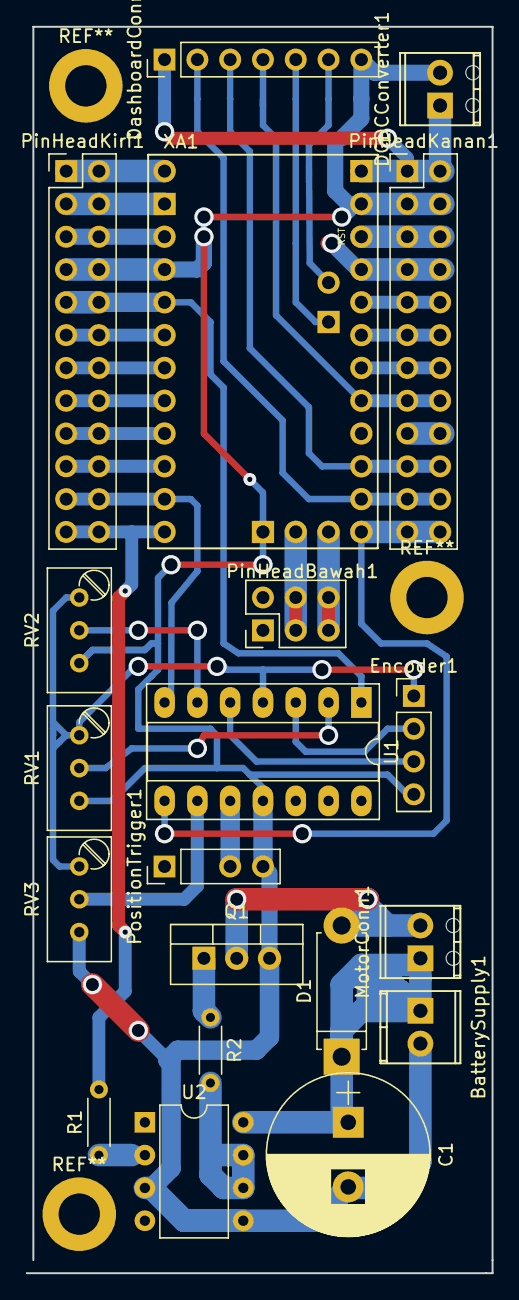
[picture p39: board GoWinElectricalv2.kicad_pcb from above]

Board: 4 copper layers, 36.1 x 96.5 mm, 20 parts (0 on the bottom side), 37 nets.

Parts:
BatterySupply1: Conn_1x2; TerminalBlock_Phoenix_MPT-2.54mm_2pol
C1: CP; CP_Radial_D12.5mm_P5.00mm
D1: D; D_5W_P10.16mm_Horizontal
DCDCConverter1: Conn_1x2; TerminalBlock_Phoenix_MPT-2.54mm_2pol
DashboardConn1: XH2.54_7p; Pin_Header_Straight_1x07_Pitch2.54mm
Encoder1: XH2.54_4p; Pin_Header_Straight_1x04_Pitch2.54mm
MotorConn1: Conn_1x2; TerminalBlock_Phoenix_MPT-2.54mm_2pol
PinHeadBawah1: Conn_02x03_Odd_Even; Pin_Header_Straight_2x03_Pitch2.54mm
PinHeadKanan1: Conn_02x12_Odd_Even; Pin_Header_Straight_2x12_Pitch2.54mm
PinHeadKiri1: Conn_02x12_Odd_Even; Pin_Header_Straight_2x12_Pitch2.54mm
PositionTrigger1: XH2.54_4p; Pin_Header_Straight_1x04_Pitch2.54mm
Q1: IRF3205; TO-220-3_Vertical
R1, R2: R; R_Axial_DIN0204_L3.6mm_D1.6mm_P5.08mm_Horizontal
RV1, RV2, RV3: POT_TRIM; Potentiometer_Trimmer_Bourns_3296W
U1: LM324; DIP-14_W7.62mm_Socket_LongPads
U2: HCPL3120; DIP-8_W7.62mm
XA1: Arduino_Mini_01_Socket; Arduino_Mini_Socket

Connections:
+5V: Encoder1.1, PinHeadKanan1.7, PinHeadKanan1.8, RV1.1, RV2.1, RV3.1, U1.4, XA1.5V1
+BATT: BatterySupply1.1, C1.1, D1.1, MotorConn1.1, U2.8
+VDC: DCDCConverter1.1, DashboardConn1.1, PinHeadKanan1.1, PinHeadKanan1.2, XA1.VIN
/Controller/A1: PinHeadKanan1.13, PinHeadKanan1.14, XA1.A1
/Controller/A2: PinHeadKanan1.11, PinHeadKanan1.12, XA1.A2
/Controller/A3: PinHeadKanan1.9, PinHeadKanan1.10, XA1.A3
/Controller/A6: PinHeadBawah1.3, PinHeadBawah1.4, XA1.A6
/Controller/A7: PinHeadBawah1.5, PinHeadBawah1.6, XA1.A7
/Controller/Button_User_1_IN: DashboardConn1.2, PinHeadKanan1.21, PinHeadKanan1.22, XA1.D11
/Controller/Button_User_2_IN: DashboardConn1.3, PinHeadKanan1.19, PinHeadKanan1.20, XA1.D12
/Controller/Button_User_3_IN: DashboardConn1.4, PinHeadKanan1.15, PinHeadKanan1.16, XA1.A0, XA1.D13
/Controller/D3: PinHeadKiri1.11, PinHeadKiri1.12, XA1.D3
/Controller/D4: PinHeadKiri1.13, PinHeadKiri1.14, XA1.D4
/Controller/D5: PinHeadKiri1.15, PinHeadKiri1.16, XA1.D5
/Controller/D6: PinHeadKiri1.17, PinHeadKiri1.18, XA1.D6
/Controller/D7: PinHeadKiri1.19, PinHeadKiri1.20, XA1.D7
/Controller/ENCODER_IN_Dir: PinHeadKiri1.21, PinHeadKiri1.22, U1.7, XA1.D8
/Controller/ENCODER_IN_Tick: PinHeadKiri1.9, PinHeadKiri1.10, U1.1, XA1.D2
/Controller/Encoder_Dir: Encoder1.3, U1.5
/Controller/Encoder_Tick: Encoder1.2, U1.3
/Controller/LCD_SCL: DashboardConn1.6, XA1.A5
/Controller/LCD_SDA: DashboardConn1.5, XA1.A4
/Controller/MOTOR-: D1.2, MotorConn1.2, Q1.2
/Controller/MotorPWM_OUT: PinHeadKiri1.23, PinHeadKiri1.24, R1.2, XA1.D9
/Controller/PositionTrigger: PositionTrigger1.3, U1.10
/Controller/PositionTrigger_IN: PinHeadKanan1.23, PinHeadKanan1.24, U1.8, XA1.D10
/Controller/RXI: PinHeadKiri1.3, PinHeadKiri1.4, XA1.D1
/Controller/Reset: PinHeadKanan1.5, PinHeadKanan1.6, PinHeadKiri1.5, PinHeadKiri1.6, XA1.RST2
/Controller/TXO: PinHeadKiri1.1, PinHeadKiri1.2, XA1.D0
GND: BatterySupply1.2, C1.2, DCDCConverter1.2, DashboardConn1.7, Encoder1.4, PinHeadKanan1.3, PinHeadKanan1.4, PinHeadKiri1.7, PinHeadKiri1.8, PositionTrigger1.4, Q1.3, RV1.3, RV2.3, RV3.3, U1.11, U2.3, U2.5, XA1.GND2, XA1.GND4, XA1.L0
unnamed: PinHeadKanan1.17, PinHeadKanan1.18
unnamed: Q1.1, R2.1
unnamed: R1.1, U2.2
unnamed: R2.2, U2.6, U2.7
unnamed: RV1.2, U1.2
unnamed: RV2.2, U1.6
unnamed: RV3.2, U1.9

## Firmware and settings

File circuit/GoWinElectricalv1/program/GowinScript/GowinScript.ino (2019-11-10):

#include <Wire.h> 
#include <LiquidCrystal_I2C.h>
// The menu wrapper library
#include <LiquidMenu.h>

LiquidCrystal_I2C lcd(0x27,16,2);

/*
 * Variables used for periodic execution of code. The first one is the period
 * in milliseconds and the second one is the last time the code executed.
 */

/// Editable Program
//Init Variabel
double jarak = 0;
double djarak = 0;
double jumlahDropbiji = 0;
double jarakAntarTick = 0.1; // satuan cm
double jarakAntarBiji = 4; // satuan cm
int setup_var = 2;

/*
 * LiquidLine objects represent a single line of text and/or variables
 * on the display. The first two parameters are the column and row from
 * which the line starts, the rest of the parameters are the text and/or
 * variables that will be printed on the display. They can be up to four.
 */
// Here the line is set to column 1, row 0 and will print the passed
// string and the passed variable.
LiquidLine Running_line1(1, 0, "Jarak :", jarak);
// Here the column is 3, the row is 1 and the string is "Hello Menu".
LiquidLine Running_line2(1, 1, "Drop :", jumlahDropbiji);

/*
 * LiquidScreen objects represent a single screen. A screen is made of
 * one or more LiquidLine objects. Up to four LiquidLine objects can
 * be inserted from here, but more can be added later in setup() using
 * welcome_screen.add_line(someLine_object);.
 */
// Here the LiquidLine objects are the two objects from above.
LiquidScreen Running_screen(Running_line1, Running_line2);

// Here there is not only a text string but also a changing integer variable.
LiquidLine JarakAntarTick_line(0, 0, "Tick: ", jarakAntarTick);
LiquidScreen Setup_screen(JarakAntarTick_line);

// Here there is not only a text string but also a changing integer variable.
LiquidLine JarakAntarBiji_line(0, 0, "Biji: ", jarakAntarBiji);
LiquidScreen Setup_Second_screen(JarakAntarBiji_line);

/*
 * The LiquidMenu object combines the LiquidScreen objects to form the
 * menu. Here it is only instantiated and the screens are added later
 * using menu.add_screen(someScreen_object);. This object is used to
 * control the menu, for example: menu.next_screen(), menu.switch_focus()...
 */
LiquidMenu menu(lcd);

// PIN Define
#define EncoderTickPin 2
#define EncoderDirPin 8
#define EncoderDir 1
#define PositionTrig 10

#define Dashboard_Button1 11
#define Dashboard_Button2 12
#define Dashboard_Button3 A0

#define Reset_Button Dashboard_Button3
#define Setup_Button Dashboard_Button1

#define Select_Button Dashboard_Button1
#define Up_Button Dashboard_Button2
#define Down_Button Dashboard_Button3

#define Motor_PWM 9


// STATE of GOWIN
enum Gowin_State{
  init_gowin,
  running_gowin,
  setup_gowin
  };

Gowin_State state_now = init_gowin;



void setup() {
  // initialize digital pin LED_BUILTIN as an output.
//  pinMode(LED_BUILTIN, OUTPUT);

  //INITIALIZATION
  pinMode(EncoderTickPin, INPUT_PULLUP);
  pinMode(EncoderDirPin, INPUT_PULLUP);
  pinMode(PositionTrig, INPUT);
  pinMode(Dashboard_Button1, INPUT_PULLUP);
  pinMode(Dashboard_Button2, INPUT_PULLUP);
  pinMode(Dashboard_Button3, INPUT_PULLUP);
  pinMode(Motor_PWM, OUTPUT);

  lcd.init();                      // initialize the lcd 
  lcd.init();
  // Print a message to the LCD.
  lcd.backlight();
  lcd.setCursor(0,0);
  lcd.print("Gowin");

  attachInterrupt(digitalPinToInterrupt(EncoderTickPin),encoderTick,RISING);
  Serial.begin(9600);

  // Menu initialization.
  menu.init();

  // This is the method used to add a screen object to the menu.
  menu.add_screen(Running_screen);
  menu.add_screen(Setup_screen);
  menu.add_screen(Setup_Second_screen);
  
  
}

// the loop function runs over and over again forever
void loop() {
  switch(state_now){
    case init_gowin:
      init_state();
      state_now = running_gowin;
      menu.change_screen(1);
      break;
    case running_gowin:
      running_state();
      if(digitalRead(Setup_Button) == 0){
        state_now = setup_gowin;
        setup_var = 2;
        menu.change_screen(2);
        delay(500);
      }      
      Serial.println("Running");
      break;
    case setup_gowin:
      setup_state();
      if((digitalRead(Up_Button) == 0) && (digitalRead(Down_Button) == 0)){
        state_now = running_gowin;
        menu.change_screen(1);
        delay(500);
      }      
      break;
  }
}

void init_state(){
  Serial.println("INIT State");
  delay(1000);
}

void running_state(){
  delay(100);
  menu.update();
  if(digitalRead(Reset_Button) == 0){
    jarak = 0;
    jumlahDropbiji = 0;
    Serial.println("RESET");
  }

  
  if(((int(jarak) % int(jarakAntarBiji)) == 0 ) && (djarak > 0) && (jarak != 0)){
    // DropBiji
    ///Jalankan Motor
    analogWrite(Motor_PWM,255);
    delay(100);
    while(digitalRead(PositionTrig) == 0){
      Serial.println("MotorBerputar");   
    }
    analogWrite(Motor_PWM,0);
    jumlahDropbiji = jumlahDropbiji + 1;
  }

  
  
  Serial.print("Jarak : ");Serial.print(jarak);
  Serial.print(" DropBiji : ");Serial.println(jumlahDropbiji);
//  delay(100);
}

void setup_state(){
  delay(100);
  menu.update();
  if(digitalRead(Select_Button) == 0){
    
    switch(setup_var){
      case 2:
        menu.change_screen(3);
        setup_var = 3;
        break;
      case 3:
        menu.change_screen(2);
        setup_var = 2;
        break;
    }
  }
  switch(setup_var){
      case 2:
        if(digitalRead(Up_Button) == 0){
          jarakAntarTick = jarakAntarTick + 0.1;
          delay(100);
        }else if(digitalRead(Down_Button) == 0){
          jarakAntarTick = jarakAntarTick - 1;
        }
        Serial.println("SET JARAK");
        break;
      case 3:
        if(digitalRead(Up_Button) == 0){
          jarakAntarBiji = jarakAntarBiji + 1;
        }else if(digitalRead(Down_Button) == 0){
          jarakAntarBiji = jarakAntarBiji - 1;
        }
        Serial.println("SET BIJI");
        break;
    }
  
//  Serial.println("SETUP");
}
void encoderTick(){
  if(digitalRead(EncoderDirPin)){
    djarak = (jarak + (EncoderDir*jarakAntarTick)) - jarak;
    jarak = jarak + (EncoderDir*jarakAntarTick);   
  }else{
    djarak = (jarak - (EncoderDir*jarakAntarTick)) - jarak;
    jarak = jarak - (EncoderDir*jarakAntarTick);
    
    }  
  if(djarak > 0){
    Serial.println("maju");  
  }else{
    Serial.println("mundur");
  }
}

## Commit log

2019-10-04 Update Nota dan desain 3d
    [Akrilik.dxf, Coupler.FCStd, DropperBiji.FCStd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]
2019-11-07 Update dokumentasi 07112019
    [BoxElectronic.FCStd, BoxElectronicAssembly.FCStd, BoxElectronicPart.FCStd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]
2019-11-10 Update 11_11_2019
    [Dashboard.sch, GoWin Electrical.kicad_pcb, GoWin Electrical.sch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]
